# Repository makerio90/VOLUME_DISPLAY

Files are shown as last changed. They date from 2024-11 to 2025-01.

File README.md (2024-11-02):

# VOLUME_DISPLAY
this is a project i have been working on for the better part of a month now, this is only the first commit as i have dicided to add the project to github.

## The Idea:
i wanted to make a volumetric pov display. i got insperation from these projects:

- [this project is what kicked it off](https://hackaday.com/2024/09/09/doom-on-a-volumetric-display/)
- [and this served as insperation](https://hackaday.com/2021/02/21/volumetric-3d-television-is-here/)

both work off of the same principle: phisicly rotating an led matrix to create the sense of volume.

this seemed doable so i started work on schematics.

## theory of operation
cutting to the chase here: this is what the mainboard needs to do:

the main board is intended to drive a 32x16 led matrix at a high framerate (>1000fps).
new frames will be added to a framebuffer through a rs-485 bus. 12v power will also be supplied.
a hall effect sensor will provide a sync signal, allowing the board to make minor ajustments to its framerate.
most importently, this whole board rotates around. 12v and rs485 is fed through a slipring.

the entire board must be slowed to a stop in order for the rp2040 to be programmed.
whenever the usb port is plugged in. the rp2040 will be powered and in prog mode.
*the led drivers should be off when usb is plugged in!*

the board will be in the shape of a circle. the led matrix will be mounted vertically in the center via the attached pinheders.
because the board will likely be unbalanced, nuts and bolts will be added around in a circle to provide an option for balance.

## 4-layer stackup

top: high speed traces
in 1: signal, power & ground
in 2: Ground only
BOT: low speed, high current traces.

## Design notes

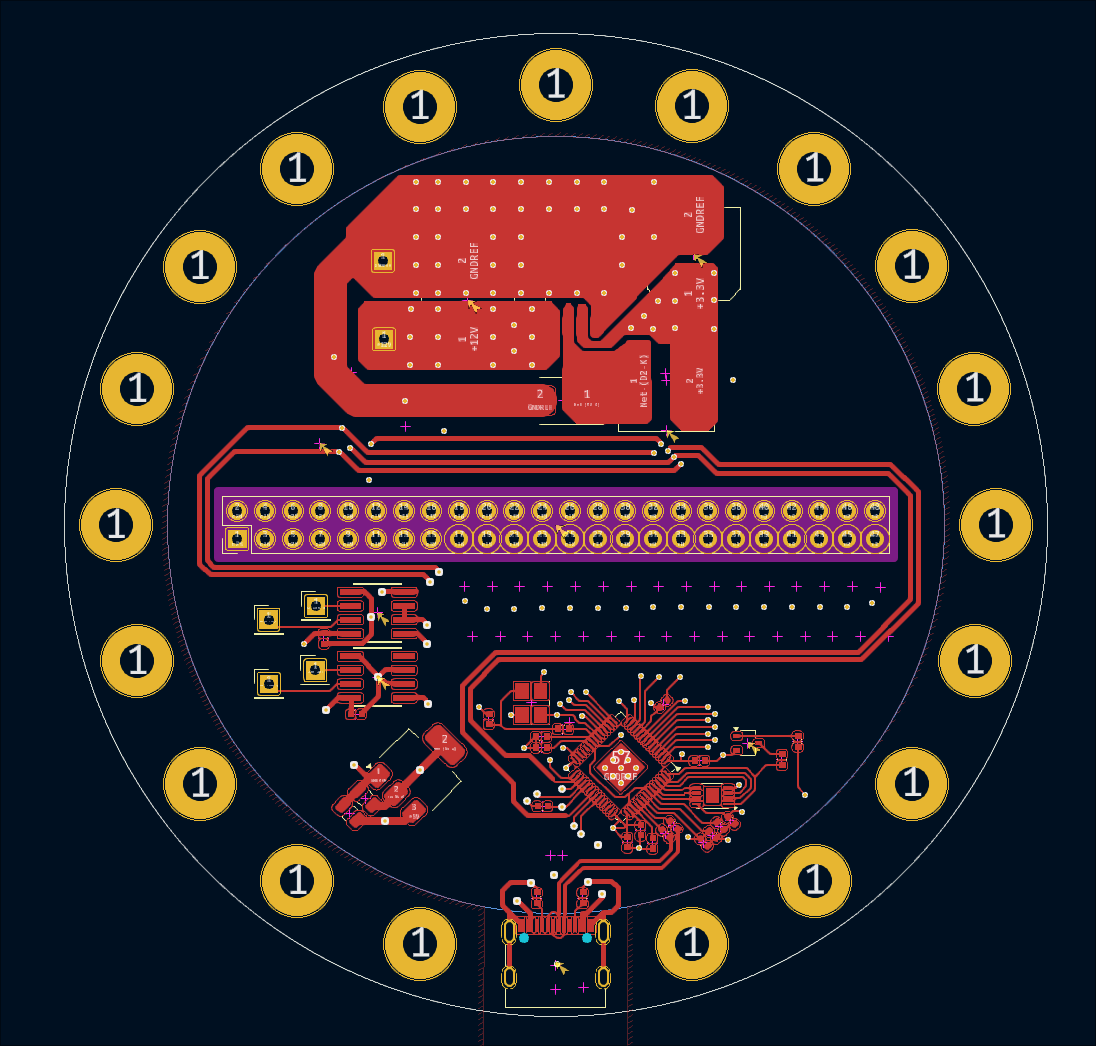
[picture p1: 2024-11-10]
forReview/TOP.png

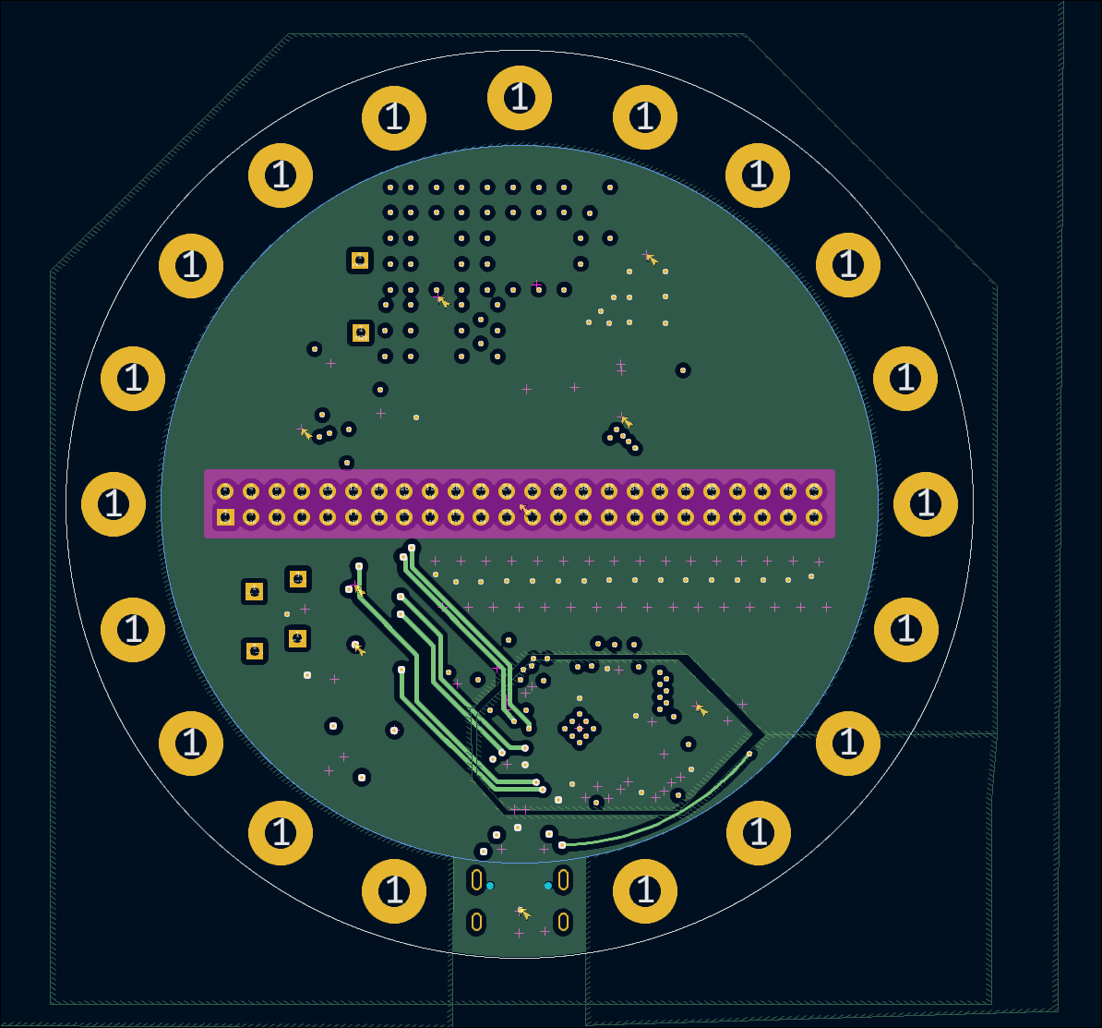
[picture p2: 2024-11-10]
forReview/in1.png

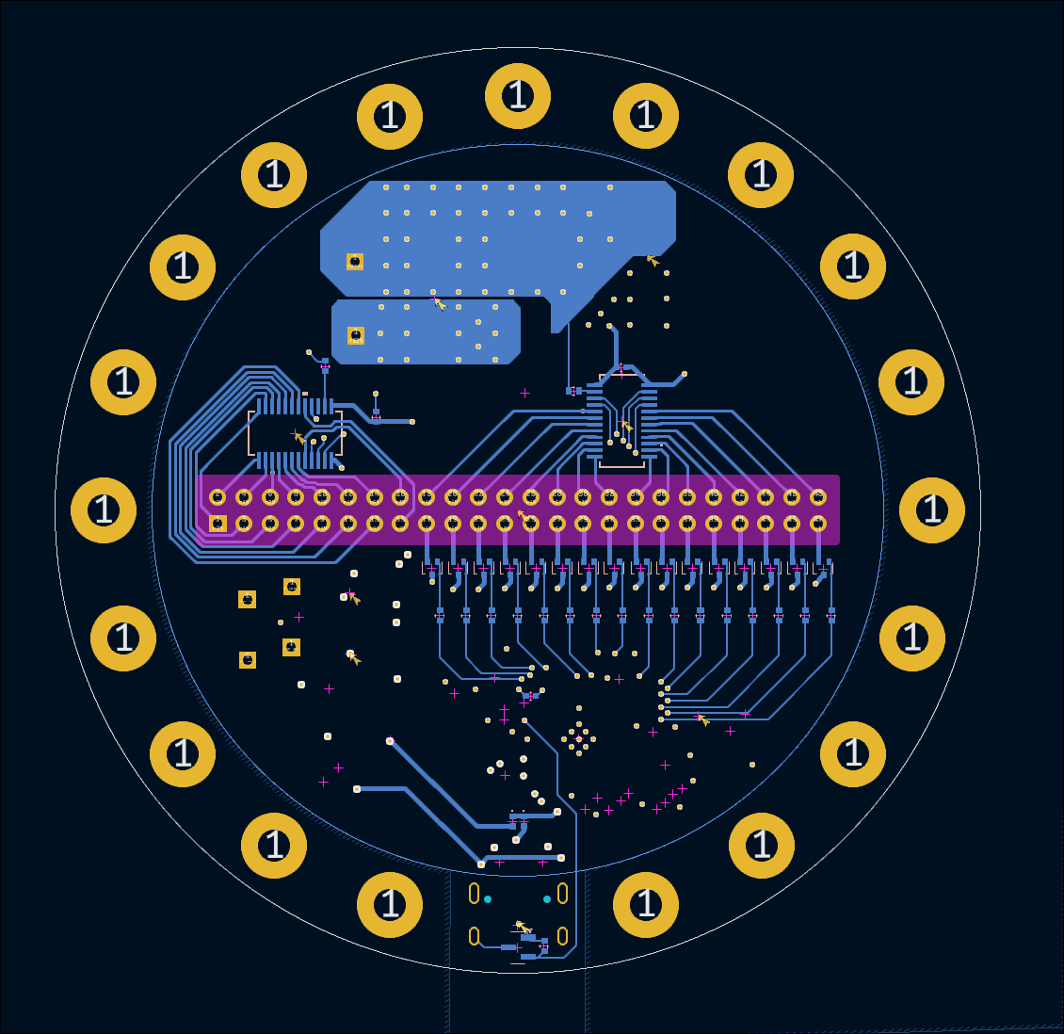
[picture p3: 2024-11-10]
forReview/BOT.png

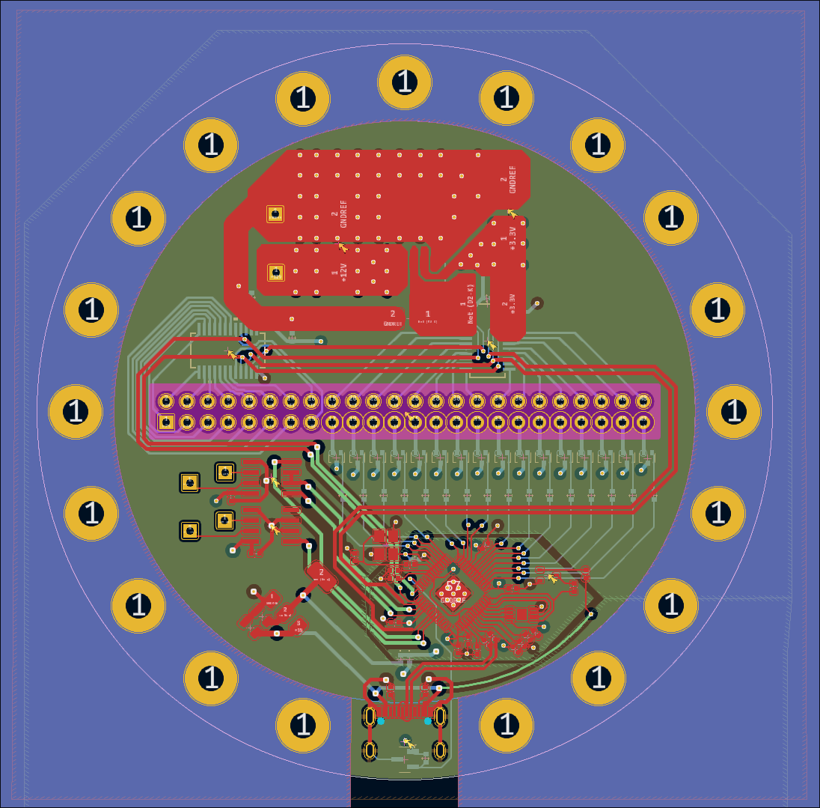
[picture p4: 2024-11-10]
forReview/all.png

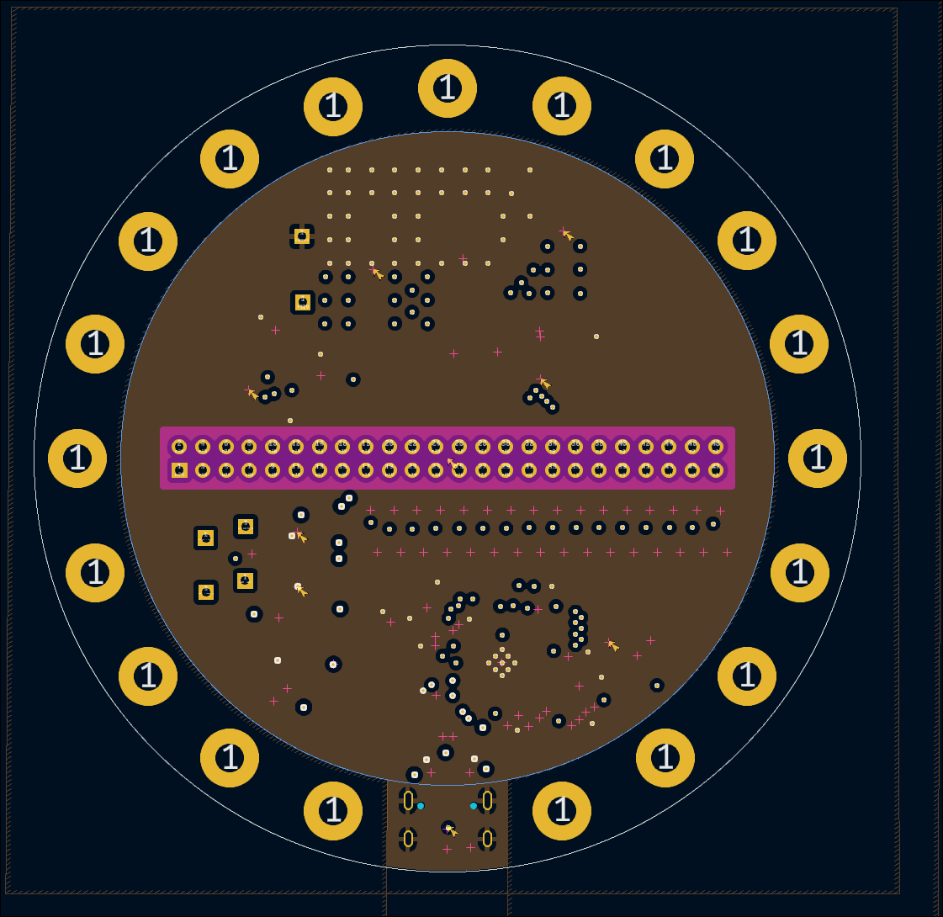
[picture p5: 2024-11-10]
forReview/in2.png

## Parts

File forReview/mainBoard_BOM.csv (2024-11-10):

Quantity | Comment | Designator | Footprint | LCSC PN | MPN | Manufacturer
2 | 10u | C1,C2 | Capacitor_SMD:C_0805_2012Metric | C15850 | CL21A106KAYNNNE | Samsung Electro-Mechanics
2 | 470uF | C16,C19 | Capacitor_SMD:C_Elec_8x10.2 | C343909 | EEEFP1C471AP | PANASONIC
2 | 15p | C17,C18 | Capacitor_SMD:C_0402_1005Metric | C307341 | CL05C150JB51PNC | Samsung Electro-Mechanics
14 | 100n | C3,C4,C6,C8,C9,C10,C11,C12,C13,C14,C15,C20,C21,C22 | Capacitor_SMD:C_0402_1005Metric | C1525 | CL05B104KO5NNNC | Samsung Electro-Mechanics
2 | 1u | C5,C7 | Capacitor_SMD:C_0402_1005Metric | C14445 | CL05A105KP5NNNC | Samsung Electro-Mechanics
1 | D_Schottky | D2 | Diode_SMD:D_SMB | C28642302 | TPNSR05F40NXT5G | TECH PUBLIC
2 | D | D1,D3 | Diode_SMD:D_0402_1005Metric | C703125 | LQW15AN12NH00D | Murata Electronics
1 | USB_C_Receptacle_USB2.0_16P | J1 | Connector_USB:USB_C_Receptacle_G-Switch_GT-USB-7010ASV | C2988369 | GT-USB-7010ASV | G-Switch
1 | SDCHA1V8040-470-R | L1 | Inductor_SMD:L_Coilcraft_XAL8080-XXX | C17221881 | SDCHA1V8040-470-R | EATON
2 | ST3485EBDR | Mm_rs485,RX_rs485 | footprints:SO-8_STM | C75809 | ST3485EBDR | STMicroelectronics
1 | BC846B,215 | Q1 | Package_TO_SOT_SMD:SOT-323_SC-70 | C87062 | BC846B,215 | Nexperia
16 | PMOS | Q2,Q3,Q4,Q5,Q6,Q7,Q8,Q9,Q10,Q11,Q12,Q13,Q14,Q15,Q16,Q17 | Package_TO_SOT_SMD:SOT-416 | C54876 | NTA4151PT1G | onsemi
2 | 27 | R1,R5 | Resistor_SMD:R_0402_1005Metric | C384351 | WR04X270JTL | Walsin Tech Corp
2 | 5.1k | R10,R11 | Resistor_SMD:R_0402_1005Metric | C5913162 | FCR0402F5K1 | VO
4 | 1k | R2,R6,R7,R9 | Resistor_SMD:R_0402_1005Metric | C102758 | RTT02102JTH | RALEC
2 | 2.65k | R3,R4 | Resistor_SMD:R_0402_1005Metric | C321166 | RC-02U2R61FT | RC-02U2R61FT
16 | 10 | R8,R12,R13,R14,R15,R16,R17,R18,R19,R20,R21,R22,R23,R24,R25,R26 | Resistor_SMD:R_0402_1005Metric | C100206 | CR0402FF10R0G | LIZ Elec
1 | W25Q128JVS | U1 | Package_DFN_QFN:WFDFPN-8-1EP_3x2mm_P0.5mm_EP1.25x1.35mm | C190862 | W25Q128JVPIQ | Winbond Electronics
1 | NCP1117-3.3_SOT223 | U5 | Package_TO_SOT_SMD:SOT-223-3_TabPin2 | C98965 | NCP1117ST12T3G | onsemi
1 | DRV5033FAxDBZ | U6 | Package_TO_SOT_SMD:SOT-23 | C2869057 | DRV5033FAQDBZR | Texas Instruments
1 | AP1509 | U7 | Package_SO:SOP-8_5.28x5.23mm_P1.27mm | C151822 | AP1509-SG-13 | Diodes Incorporated
1 | RP2040 | U8 | Package_DFN_QFN:QFN-56-1EP_7x7mm_P0.4mm_EP3.2x3.2mm | C2040 | RP2040 | Raspberry Pi
2 | TLC59283DBQR | U3,U4 | DBQ24_TEX:DBQ24_TEX | C702075 | TLC59283DBQR | Texas Instruments
1 | ABM8-272-T3 | Y2 | Crystal:Crystal_SMD_3225-4Pin_3.2x2.5mm | C20625731 | ABM8-272-T3 | Abracon LLC

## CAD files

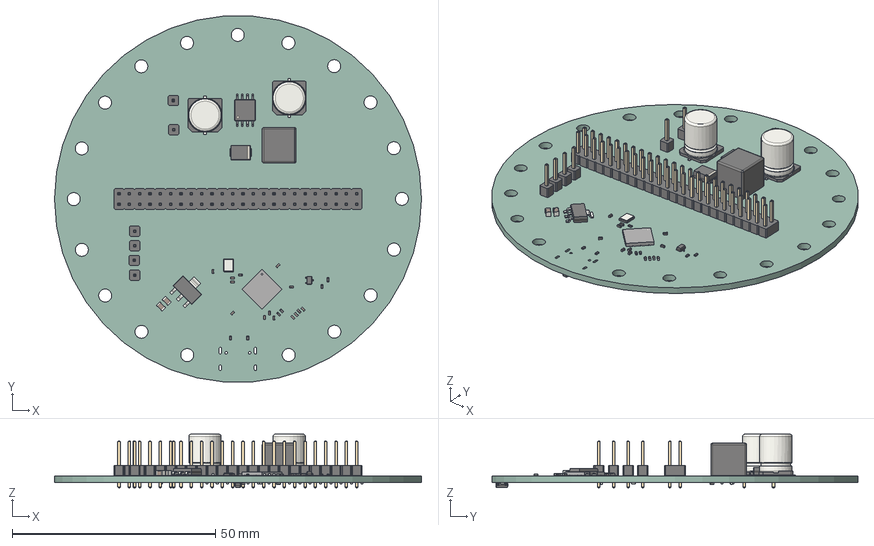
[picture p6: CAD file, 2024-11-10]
mainBoard.step
90.2 x 89.9 x 13.2 mm
CQ assembly
SOT_323_SC_70
C_0402_1005Metric x 16
C_Elec_8x102 x 2
R_0402_1005Metric x 26
C_0805_2012Metric x 2
PinHeader_2x24_P254mm_Vertical
Crystal_SMD_3225-4Pin_3.2x2.5mm
PinHeader_1x01_P254mm_Vertical x 6
D_SMB
SOP-8_5.28x5.23mm_P1.27mm
QFN_56_1EP_7x7mm_P04mm_EP32x32mm
SOT_223
SOT_23
mainBoard_PCB

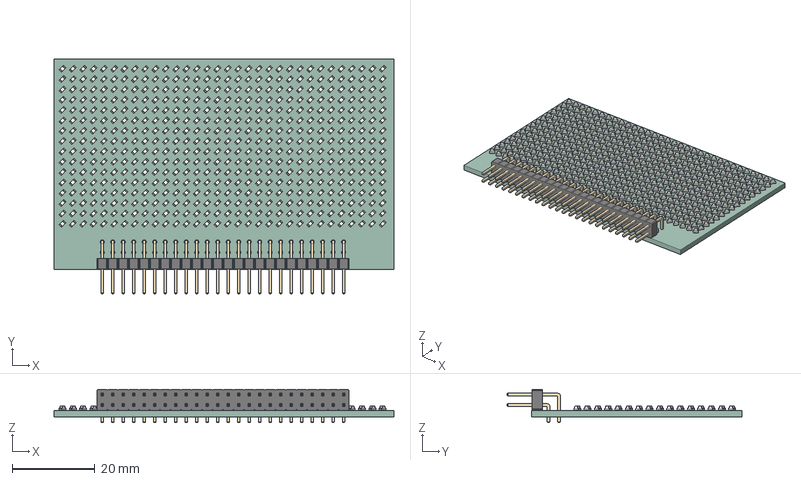
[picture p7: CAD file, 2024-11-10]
Matrix.step
82.3 x 56.8 x 8.08 mm
LED_0603_1608Metric x 512
PinHeader_2x24_P254mm_Horizontal
Matrix_PCB

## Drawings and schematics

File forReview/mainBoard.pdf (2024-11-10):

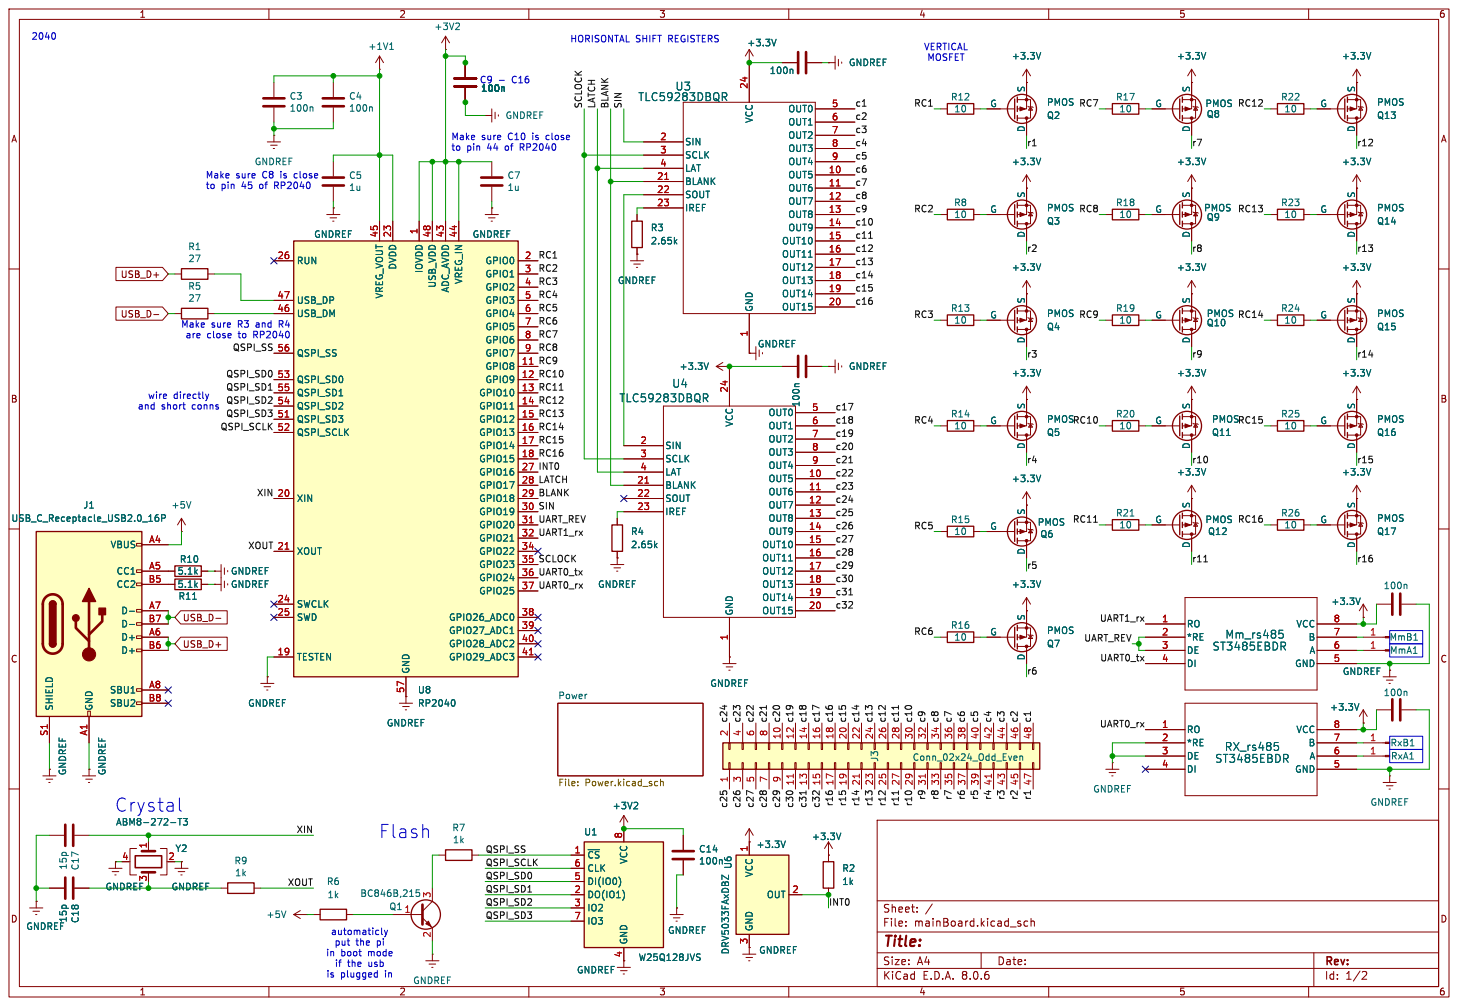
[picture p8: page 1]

HORISONTAL SHIFT REGISTERS wire directly and short conns Make sure C8 is close

to pin 45 of RP2040 Make sure R3 and R4

1 GPIO8 11 GPIO9 12 GPIO10 13 GPIO11 14 GPIO12 15 GPIO13 16 GPIO14 17 GPIO15 18 TESTEN 19 GPIO0 2 XIN 20 XOUT 21 DVDD 23 SWCLK 24 SWD 25 RUN 26 GPIO16 27 GPIO17 28 GPIO18 29 GPIO1 3 GPIO19 30 GPIO20 31 GPIO21 32 GPIO22 34 GPIO23 35 GPIO24 36 GPIO25 37 GPIO26_ADC0 38 GPIO27_ADC1 39 GPIO2 4 GPIO28_ADC2 40 GPIO29_ADC3 41 ADC_AVDD 43 VREG_IN 44 VREG_VOUT 45 USB_DM 46 USB_DP 47 USB_VDD 48 GPIO3 5 QSPI_SD3 51 QSPI_SCLK 52 QSPI_SD0 53 QSPI_SD2 54 QSPI_SD1 55 QSPI_SS 56 GND 57 GPIO4 6 GPIO5 7 GPIO6 8 GPIO7 9 U8 RP2040

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

Id: 1/2 Title: File: mainBoard.kicad_sch Sheet: / Power File: Power.kicad_sch

is plugged in Crystal

automaticly put the pi

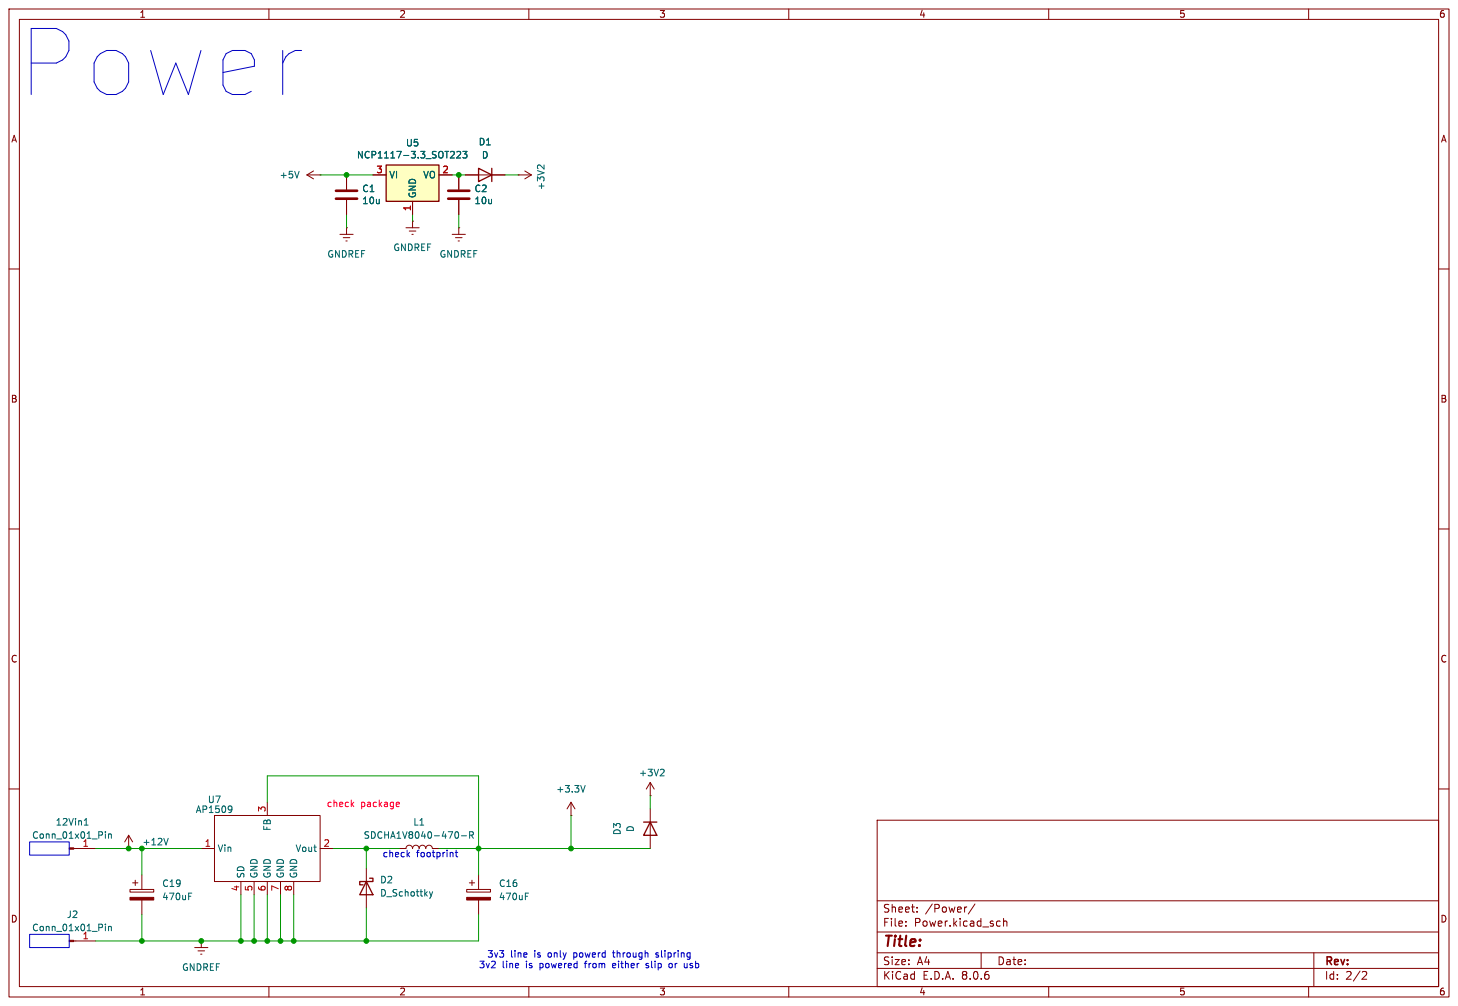
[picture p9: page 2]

Id: 2/2 Title: File: Power.kicad_sch Sheet: /Power/ D3D GNDREF GNDREF C1

check footprint check package

3v3 line is only powerd through slipring
3v2 line is powered from either slip or usb

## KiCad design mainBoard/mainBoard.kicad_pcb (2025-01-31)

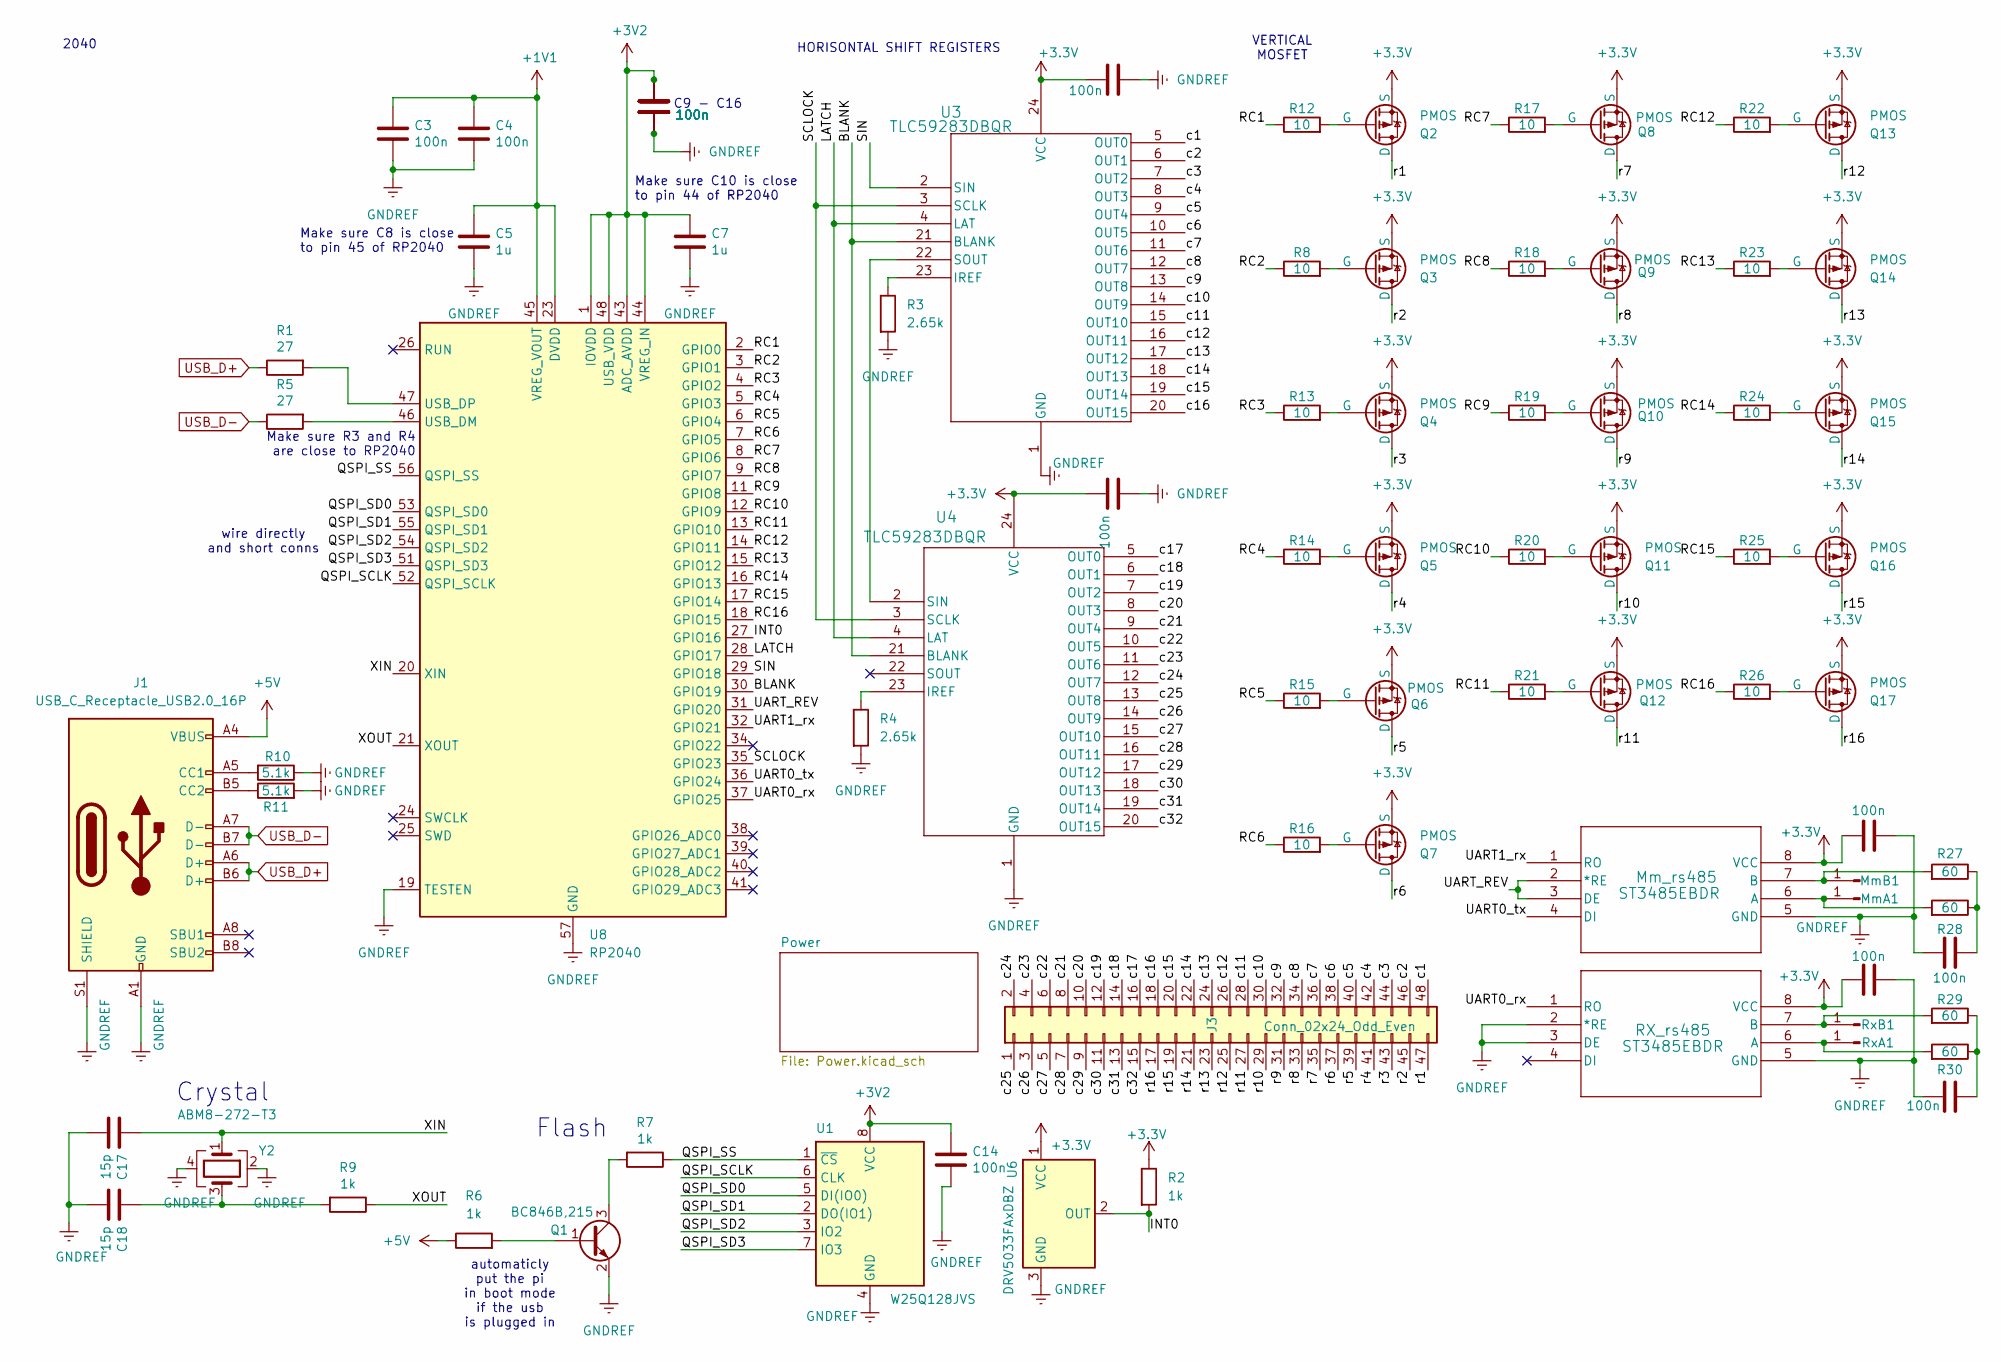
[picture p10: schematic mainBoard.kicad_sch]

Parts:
C3, C4, C6, C8, C9, C10, C11, C12, C13, C14, C15, C20, C21, C22, C23, C24: 100n; C_0402_1005Metric; MPN CL05B104KO5NNNC; LCSC PN C1525
C5, C7: 1u; C_0402_1005Metric; MPN CL05A105KP5NNNC; LCSC PN C14445
C17, C18: 15p; C_0402_1005Metric; MPN CL05C150JB51PNC; LCSC PN C307341
J1: USB_C_Receptacle_USB2.0_16P; USB_C_Receptacle_G-Switch_GT-USB-7010ASV; MPN GT-USB-7010ASV; LCSC PN C2988369
J3: Conn_02x24_Odd_Even; PinHeader_2x24_P2.54mm_Vertical
MmA1: Conn_01x01_Pin; PinHeader_1x01_P2.54mm_Vertical
MmB1: Conn_01x01_Pin; PinHeader_1x01_P2.54mm_Vertical
Mm_rs485: ST3485EBDR; SO-8_STM; MPN ST3485EBDR; LCSC PN C75809
Q1: BC846B,215; SOT-323_SC-70; MPN BC846B,215; LCSC PN C87062
Q2, Q3, Q4, Q5, Q6, Q7, Q8, Q9, Q10, Q11, Q12, Q13, Q14, Q15, Q16, Q17: PMOS; SOT-416; MPN NTA4151PT1G; LCSC PN C54876
R1, R5: 27; R_0402_1005Metric; MPN WR04X270JTL; LCSC PN C384351
R2, R6, R7, R9: 1k; R_0402_1005Metric; MPN RTT02102JTH; LCSC PN C102758
R3, R4: 2.65k; R_0402_1005Metric; MPN RC-02U2R61FT; LCSC PN C321166
R8, R12, R13, R14, R15, R16, R17, R18, R19, R20, R21, R22, R23, R24, R25, R26: 10; R_0402_1005Metric; MPN CR0402FF10R0G; LCSC PN C100206
R10, R11: 5.1k; R_0402_1005Metric; MPN FCR0402F5K1; LCSC PN C5913162
R27, R28, R29, R30: 60; R_0402_1005Metric; MPN CC0402KRX7R7BB104; LCSC PN C60474
RX_rs485: ST3485EBDR; SO-8_STM; MPN ST3485EBDR; LCSC PN C75809
RxA1: Conn_01x01_Pin; PinHeader_1x01_P2.54mm_Vertical
RxB1: Conn_01x01_Pin; PinHeader_1x01_P2.54mm_Vertical
U1: W25Q128JVS; WFDFPN-8-1EP_3x2mm_P0.5mm_EP1.25x1.35mm; MPN W25Q128JVPIQ; LCSC PN C190862
U3, U4: TLC59283DBQR; DBQ24_TEX; MPN TLC59283DBQR; LCSC PN C702075
U6: DRV5033FAxDBZ; SOT-23; MPN DRV5033FAQDBZR; LCSC PN C2869057
U8: RP2040; QFN-56-1EP_7x7mm_P0.4mm_EP3.2x3.2mm; MPN RP2040; LCSC PN C2040
Y2: ABM8-272-T3; Crystal_SMD_3225-4Pin_3.2x2.5mm; MPN ABM8-272-T3; LCSC PN C20625731

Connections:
+1V1: C3.1, C4.1, C5.1, U8.23 (DVDD), U8.45 (VREG_VOUT), U8.50 (DVDD)
+3.3V: C15.2, C20.2, C21.2, C22.2, Mm_rs485.8 (VCC), Q2.3 (S), Q3.3 (S), Q4.3 (S), Q5.3 (S), Q6.3 (S), Q7.3 (S), Q8.3 (S), Q9.3 (S), Q10.3 (S), Q11.3 (S), Q12.3 (S), Q13.3 (S), Q14.3 (S), Q15.3 (S), Q16.3 (S), Q17.3 (S), R2.1, RX_rs485.8 (VCC), U3.24 (VCC), U4.24 (VCC), U6.1 (VCC); also elsewhere on the board
+3V2: C6.1, C7.1, C8.1, C9.1, C10.1, C11.1, C12.1, C13.1, C14.1, U1.8 (VCC), U8.1 (IOVDD), U8.10 (IOVDD), U8.22 (IOVDD), U8.33 (IOVDD), U8.42 (IOVDD), U8.43 (ADC_AVDD), U8.44 (VREG_IN), U8.48 (USB_VDD), U8.49 (IOVDD); also elsewhere on the board
+5V: J1.A4 (VBUS), J1.A9 (VBUS), J1.B4 (VBUS), J1.B9 (VBUS), R6.1; also elsewhere on the board
/INT0: R2.2, U6.2 (OUT), U8.27 (GPIO16)
/LATCH: U3.4 (LAT), U4.4 (LAT), U8.28 (GPIO17)
/QSPI_SCLK: U1.6 (CLK), U8.52 (QSPI_SCLK)
/QSPI_SD0: U1.5 (DI(IO0)), U8.53 (QSPI_SD0)
/QSPI_SD1: U1.2 (DO(IO1)), U8.55 (QSPI_SD1)
/QSPI_SD2: U1.3 (IO2), U8.54 (QSPI_SD2)
/QSPI_SD3: U1.7 (IO3), U8.51 (QSPI_SD3)
/QSPI_SS: R7.1, U1.1 (~CS), U8.56 (QSPI_SS)
/RC1: R12.1, U8.2 (GPIO0)
/RC2: R8.1, U8.3 (GPIO1)
/RC3: R13.1, U8.4 (GPIO2)
/RC4: R14.1, U8.5 (GPIO3)
/RC5: R15.1, U8.6 (GPIO4)
/RC6: R16.1, U8.7 (GPIO5)
/RC7: R17.1, U8.8 (GPIO6)
/RC8: R18.1, U8.9 (GPIO7)
/RC9: R19.1, U8.11 (GPIO8)
/RC10: R20.1, U8.12 (GPIO9)
/RC11: R21.1, U8.13 (GPIO10)
/RC12: R22.1, U8.14 (GPIO11)
/RC13: R23.1, U8.15 (GPIO12)
/RC14: R24.1, U8.16 (GPIO13)
/RC15: R25.1, U8.17 (GPIO14)
/RC16: R26.1, U8.18 (GPIO15)
/SCLOCK: U3.3 (SCLK), U4.3 (SCLK), U8.35 (GPIO23)
/UART0_rx: RX_rs485.1 (RO), U8.37 (GPIO25)
/UART0_tx: Mm_rs485.4 (DI), U8.36 (GPIO24)
/UART1_rx: Mm_rs485.1 (RO), U8.32 (GPIO21)
/UART_REV: Mm_rs485.2 (*RE), Mm_rs485.3 (DE), U8.31 (GPIO20)
/XIN: C17.1, U8.20 (XIN), Y2.1
/XOUT: R9.1, U8.21 (XOUT)
/c1: J3.48, U3.5 (OUT0)
/c2: J3.46, U3.6 (OUT1)
/c3: J3.44, U3.7 (OUT2)
/c4: J3.42, U3.8 (OUT3)
/c5: J3.40, U3.9 (OUT4)
/c6: J3.38, U3.10 (OUT5)
/c7: J3.36, U3.11 (OUT6)
/c8: J3.34, U3.12 (OUT7)
/c9: J3.32, U3.13 (OUT8)
/c10: J3.30, U3.14 (OUT9)
/c11: J3.28, U3.15 (OUT10)
/c12: J3.26, U3.16 (OUT11)
/c13: J3.24, U3.17 (OUT12)
/c14: J3.22, U3.18 (OUT13)
/c15: J3.20, U3.19 (OUT14)
/c16: J3.18, U3.20 (OUT15)
/c17: J3.16, U4.5 (OUT0)
/c18: J3.14, U4.6 (OUT1)
/c19: J3.12, U4.7 (OUT2)
/c20: J3.10, U4.8 (OUT3)
/c21: J3.8, U4.9 (OUT4)
/c22: J3.6, U4.10 (OUT5)
/c23: J3.4, U4.11 (OUT6)
/c24: J3.2, U4.12 (OUT7)
/c25: J3.1, U4.13 (OUT8)
/c26: J3.3, U4.14 (OUT9)
/c27: J3.5, U4.15 (OUT10)
/c28: J3.7, U4.16 (OUT11)
/c29: J3.9, U4.17 (OUT12)
/c30: J3.11, U4.18 (OUT13)
/c31: J3.13, U4.19 (OUT14)
/c32: J3.15, U4.20 (OUT15)
/r1: J3.47, Q2.1 (D)
/r2: J3.45, Q3.1 (D)
/r3: J3.43, Q4.1 (D)
/r4: J3.41, Q5.1 (D)
/r5: J3.39, Q6.1 (D)
/r6: J3.37, Q7.1 (D)
/r7: J3.35, Q8.1 (D)
/r8: J3.33, Q9.1 (D)
/r9: J3.31, Q10.1 (D)
/r10: J3.29, Q11.1 (D)
/r11: J3.27, Q12.1 (D)
/r12: J3.25, Q13.1 (D)
/r13: J3.23, Q14.1 (D)
/r14: J3.21, Q15.1 (D)
/r15: J3.19, Q16.1 (D)
/r16: J3.17, Q17.1 (D)
GNDREF: C3.2, C4.2, C5.2, C6.2, C7.2, C8.2, C9.2, C10.2, C11.2, C12.2, C13.2, C14.2, C15.1, C17.2, C18.2, C20.1, C21.1, C22.1, C23.2, C24.1, J1.A1 (GND), J1.A12 (GND), J1.B1 (GND), J1.B12 (GND), J1.S1 (SHIELD), Mm_rs485.5 (GND), Q1.2 (E), R3.2, R4.2, R10.1, R11.2, RX_rs485.2 (*RE), RX_rs485.3 (DE), RX_rs485.5 (GND), U1.4 (GND), U3.1 (GND), U4.1 (GND), U6.3 (GND), U8.19 (TESTEN), U8.57 (GND), Y2.2, Y2.4; also elsewhere on the board
unnamed: C18.1, R9.2, Y2.3
unnamed: C23.1, R27.1, R28.1
unnamed: C24.2, R29.1, R30.1
unnamed: J1.A5 (CC1), R10.2
unnamed: J1.B5 (CC2), R11.1
unnamed: MmA1.1, Mm_rs485.6 (A), R28.2
unnamed: MmB1.1, Mm_rs485.7 (B), R27.2
unnamed: Q1.1 (B), R6.2
unnamed: Q1.3 (C), R7.2
unnamed: Q2.2 (G), R12.2
unnamed: Q3.2 (G), R8.2
unnamed: Q4.2 (G), R13.2
unnamed: Q5.2 (G), R14.2
unnamed: Q6.2 (G), R15.2
unnamed: Q7.2 (G), R16.2
unnamed: Q8.2 (G), R17.2
unnamed: Q9.2 (G), R18.2
unnamed: Q10.2 (G), R19.2
unnamed: Q11.2 (G), R20.2
unnamed: Q12.2 (G), R21.2
unnamed: Q13.2 (G), R22.2
unnamed: Q14.2 (G), R23.2
unnamed: Q15.2 (G), R24.2
unnamed: Q16.2 (G), R25.2
unnamed: Q17.2 (G), R26.2
unnamed: R30.2, RX_rs485.6 (A), RxA1.1
unnamed: R29.2, RX_rs485.7 (B), RxB1.1
unnamed: R3.1, U3.23 (IREF)
unnamed: U3.22 (SOUT), U4.2 (SIN)
unnamed: R4.1, U4.23 (IREF)
unnamed: R5.2, U8.46 (USB_DM)
unnamed: R1.2, U8.47 (USB_DP)
USB_D+: J1.A6 (D+), J1.B6 (D+), R1.1
USB_D-: J1.A7 (D-), J1.B7 (D-), R5.1

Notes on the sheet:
HORISONTAL SHIFT REGISTERS
Flash
Crystal
2040
VERTICAL MOSFET
automaticly put the pi in boot mode if the usb is plugged in
Make sure C10 is close to pin 44 of RP2040
wire directly and short conns
C9 - C16
Make sure C8 is close to pin 45 of RP2040
Make sure R3 and R4 are close to RP2040

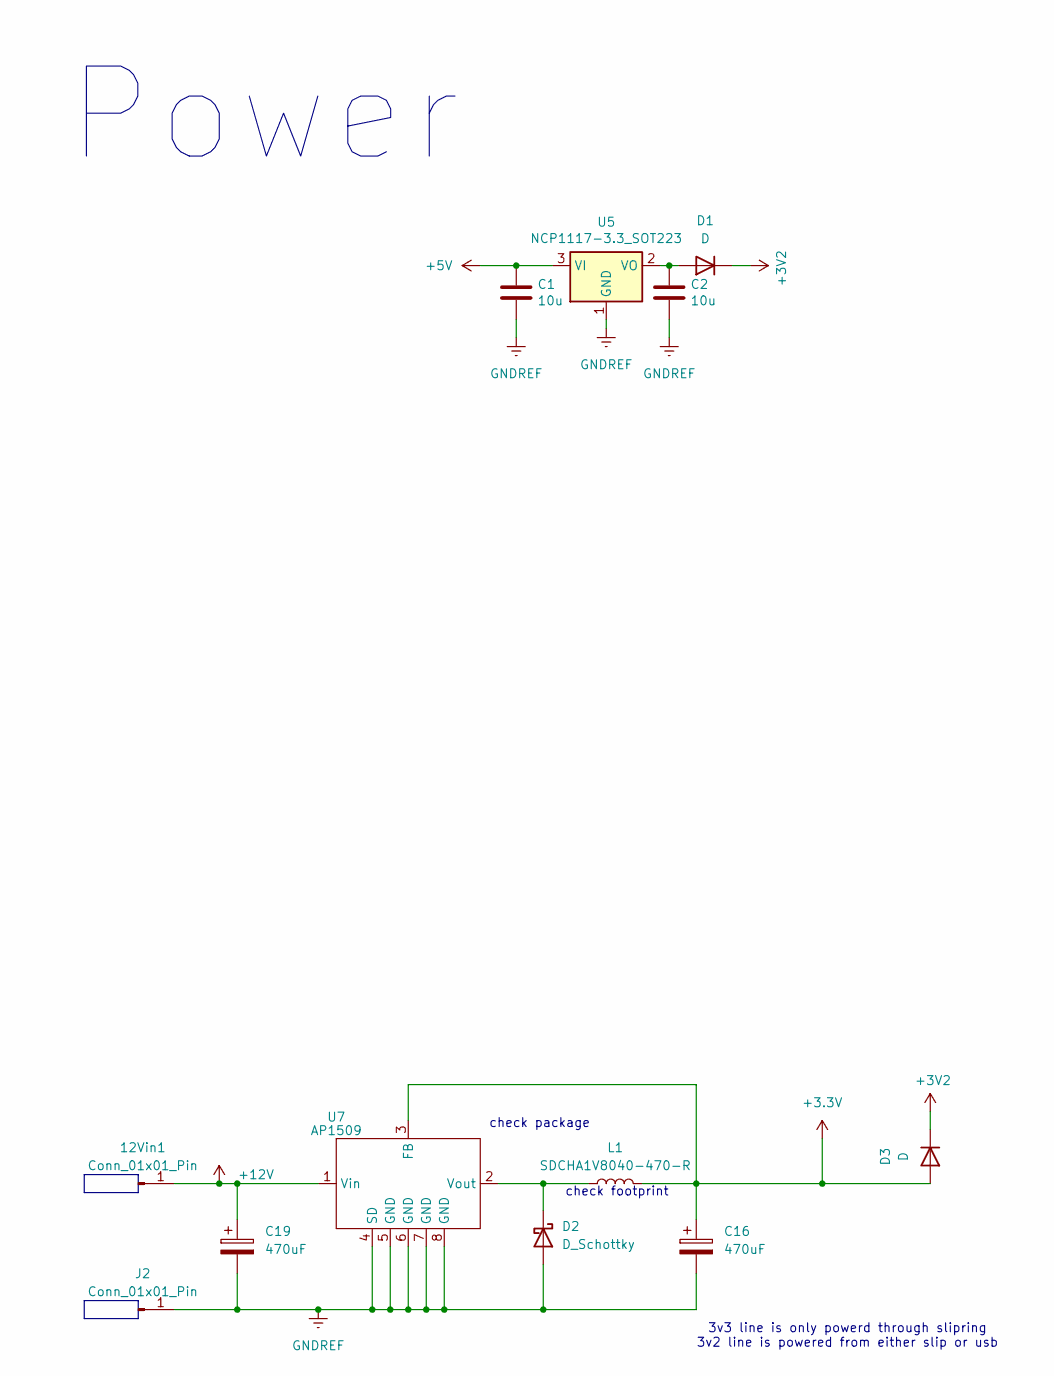
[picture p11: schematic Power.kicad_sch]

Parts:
12Vin1: Conn_01x01_Pin; PinHeader_1x01_P2.54mm_Vertical
C1, C2: 10u; C_0805_2012Metric; MPN CL21A106KAYNNNE; LCSC PN C15850
C16, C19: 470uF; C_Elec_8x10.2; MPN EEEFP1C471AP; LCSC PN C343909
D1, D3: D; D_0402_1005Metric; MPN LQW15AN12NH00D; LCSC PN C703125
D2: D_Schottky; D_SMB; MPN TPNSR05F40NXT5G; LCSC PN C28642302
J2: Conn_01x01_Pin; PinHeader_1x01_P2.54mm_Vertical
L1: SDCHA1V8040-470-R; L_Coilcraft_XAL8080-XXX; MPN SDCHA1V8040-470-R; LCSC PN C17221881
U5: NCP1117-3.3_SOT223; SOT-223-3_TabPin2; MPN NCP1117ST12T3G; LCSC PN C98965
U7: AP1509; SOP-8_5.28x5.23mm_P1.27mm; MPN AP1509-SG-13; LCSC PN C151822

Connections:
+3.3V: C16.1, D3.2 (A), L1.2, U7.3 (FB); also elsewhere on the board
+3V2: D1.1 (K), D3.1 (K); also elsewhere on the board
+5V: C1.1, U5.3 (VI); also elsewhere on the board
+12V: 12Vin1.1, C19.1, U7.1 (Vin)
GNDREF: C1.2, C2.2, C16.2, C19.2, D2.2 (A), J2.1, U5.1 (GND), U7.4 (SD), U7.5 (GND), U7.6 (GND), U7.7 (GND), U7.8 (GND); also elsewhere on the board
unnamed: C2.1, D1.2 (A), U5.2 (VO)
unnamed: D2.1 (K), L1.1, U7.2 (Vout)

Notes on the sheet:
check package
Power
check footprint
3v3 line is only powerd through slipring 3v2 line is powered from either slip or usb

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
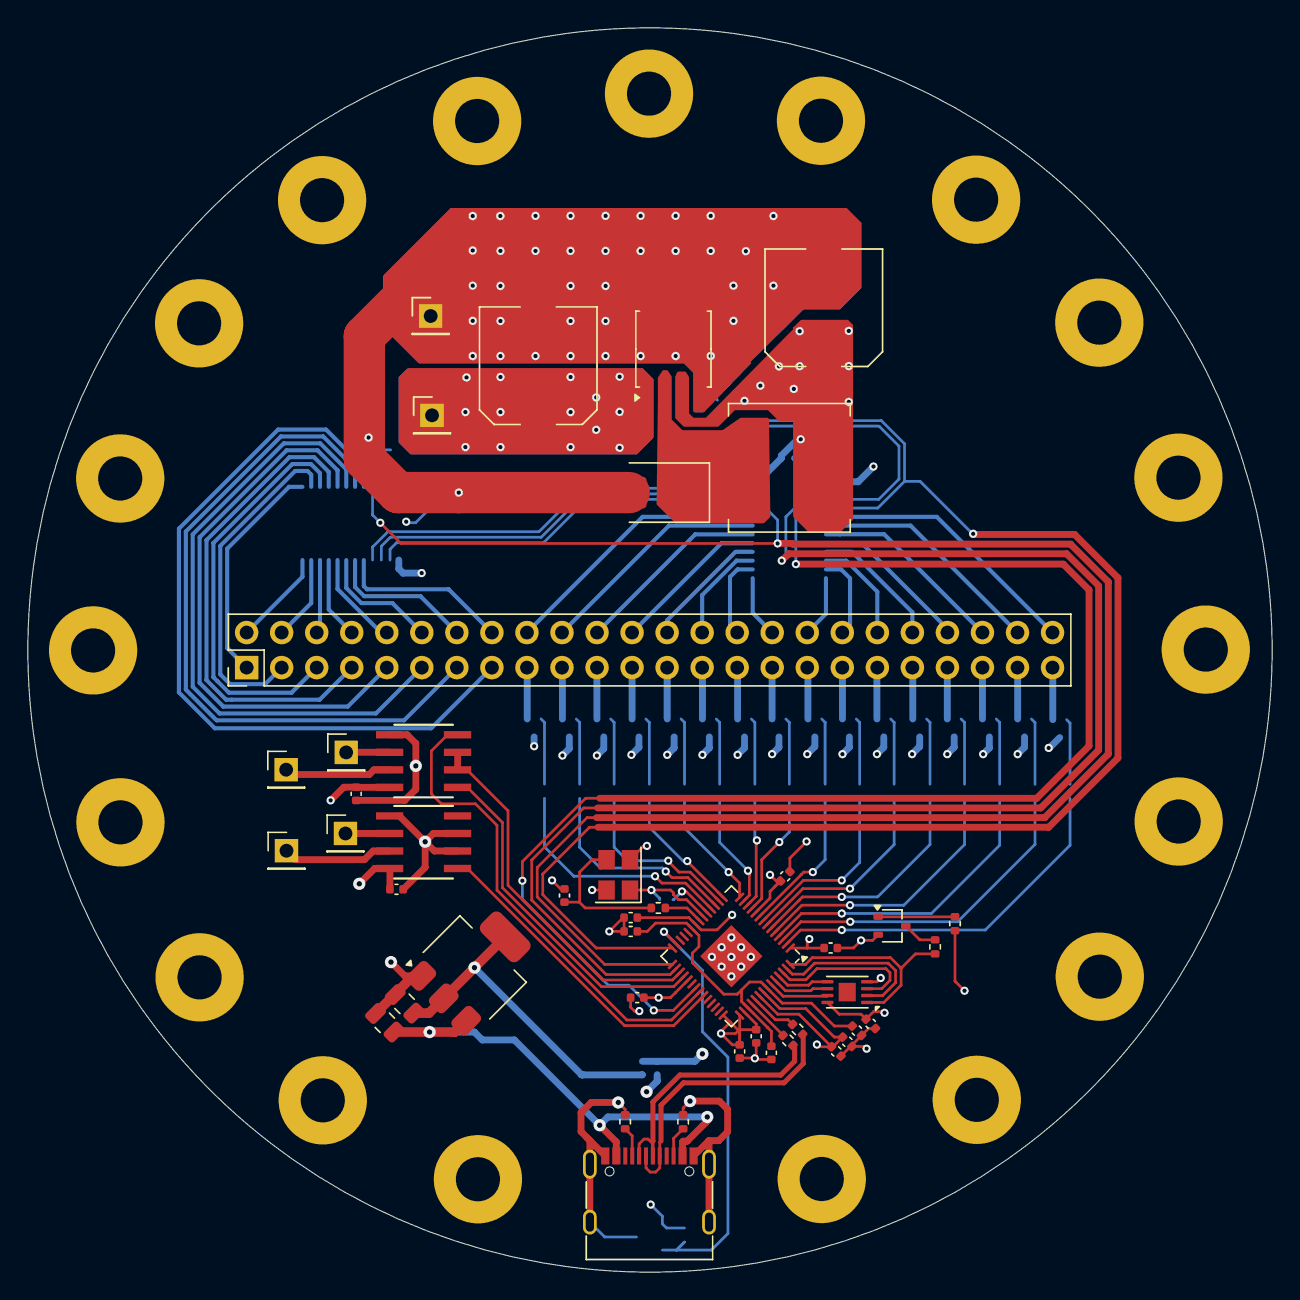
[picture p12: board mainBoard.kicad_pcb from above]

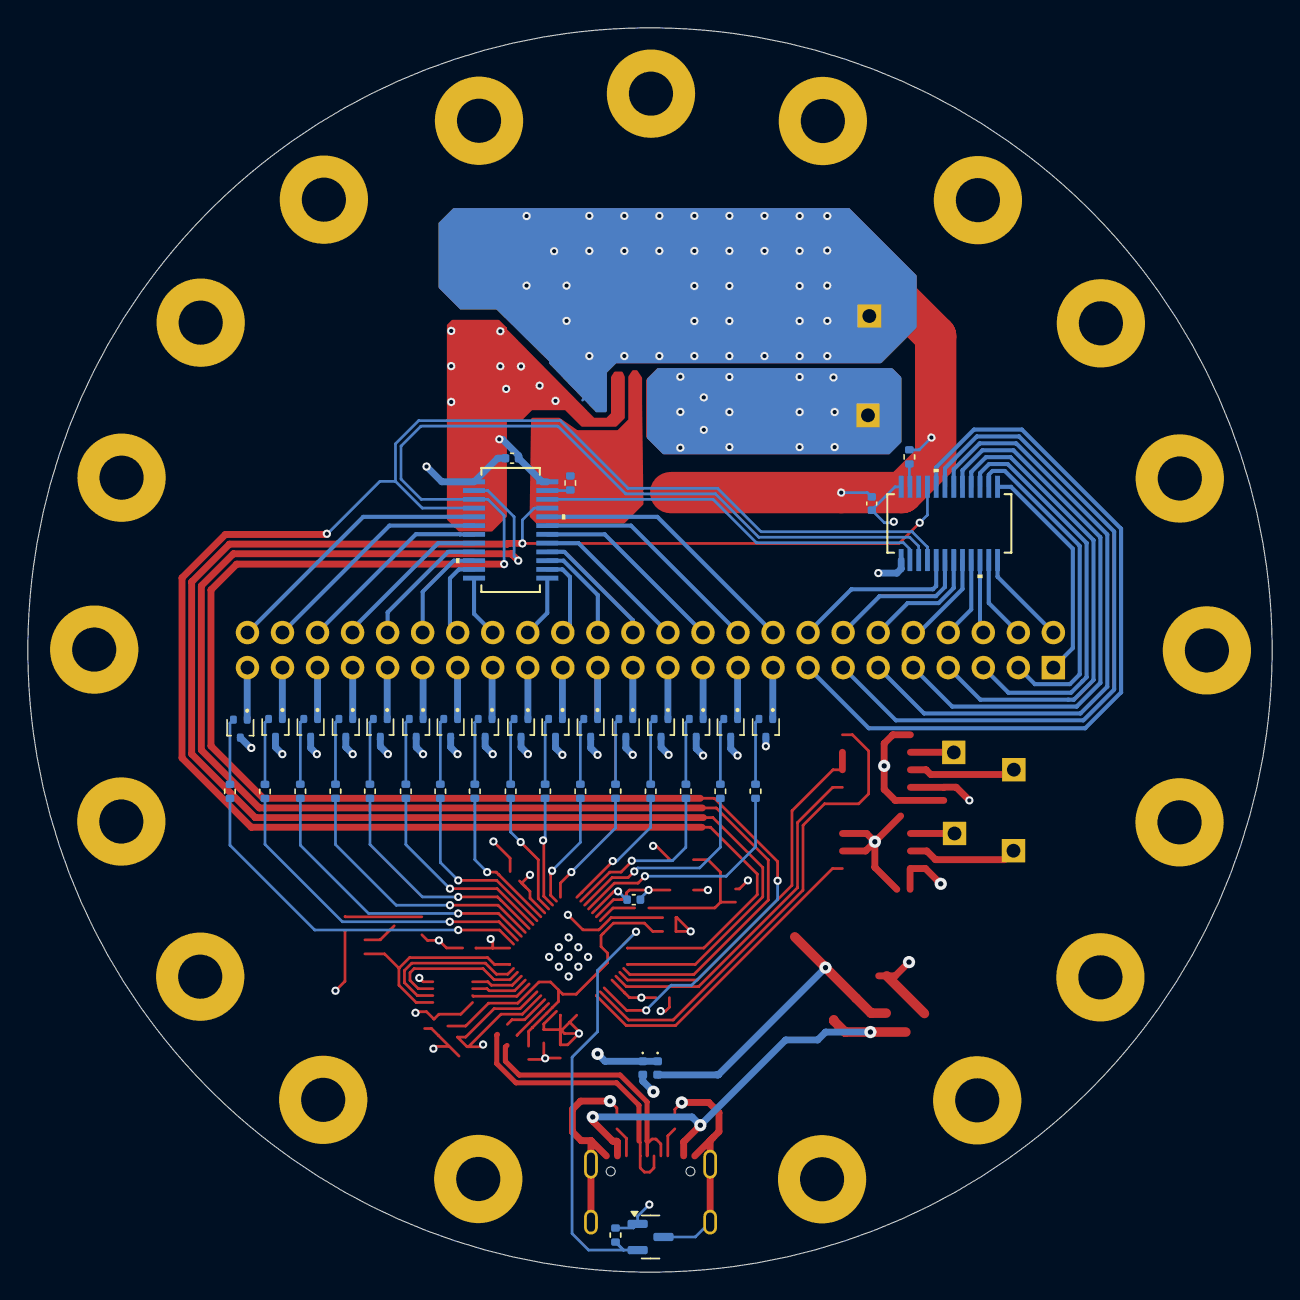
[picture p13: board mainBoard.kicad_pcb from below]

Board: 4 copper layers, 90.2 x 90.2 mm, 87 parts (43 on the bottom side), 121 nets.

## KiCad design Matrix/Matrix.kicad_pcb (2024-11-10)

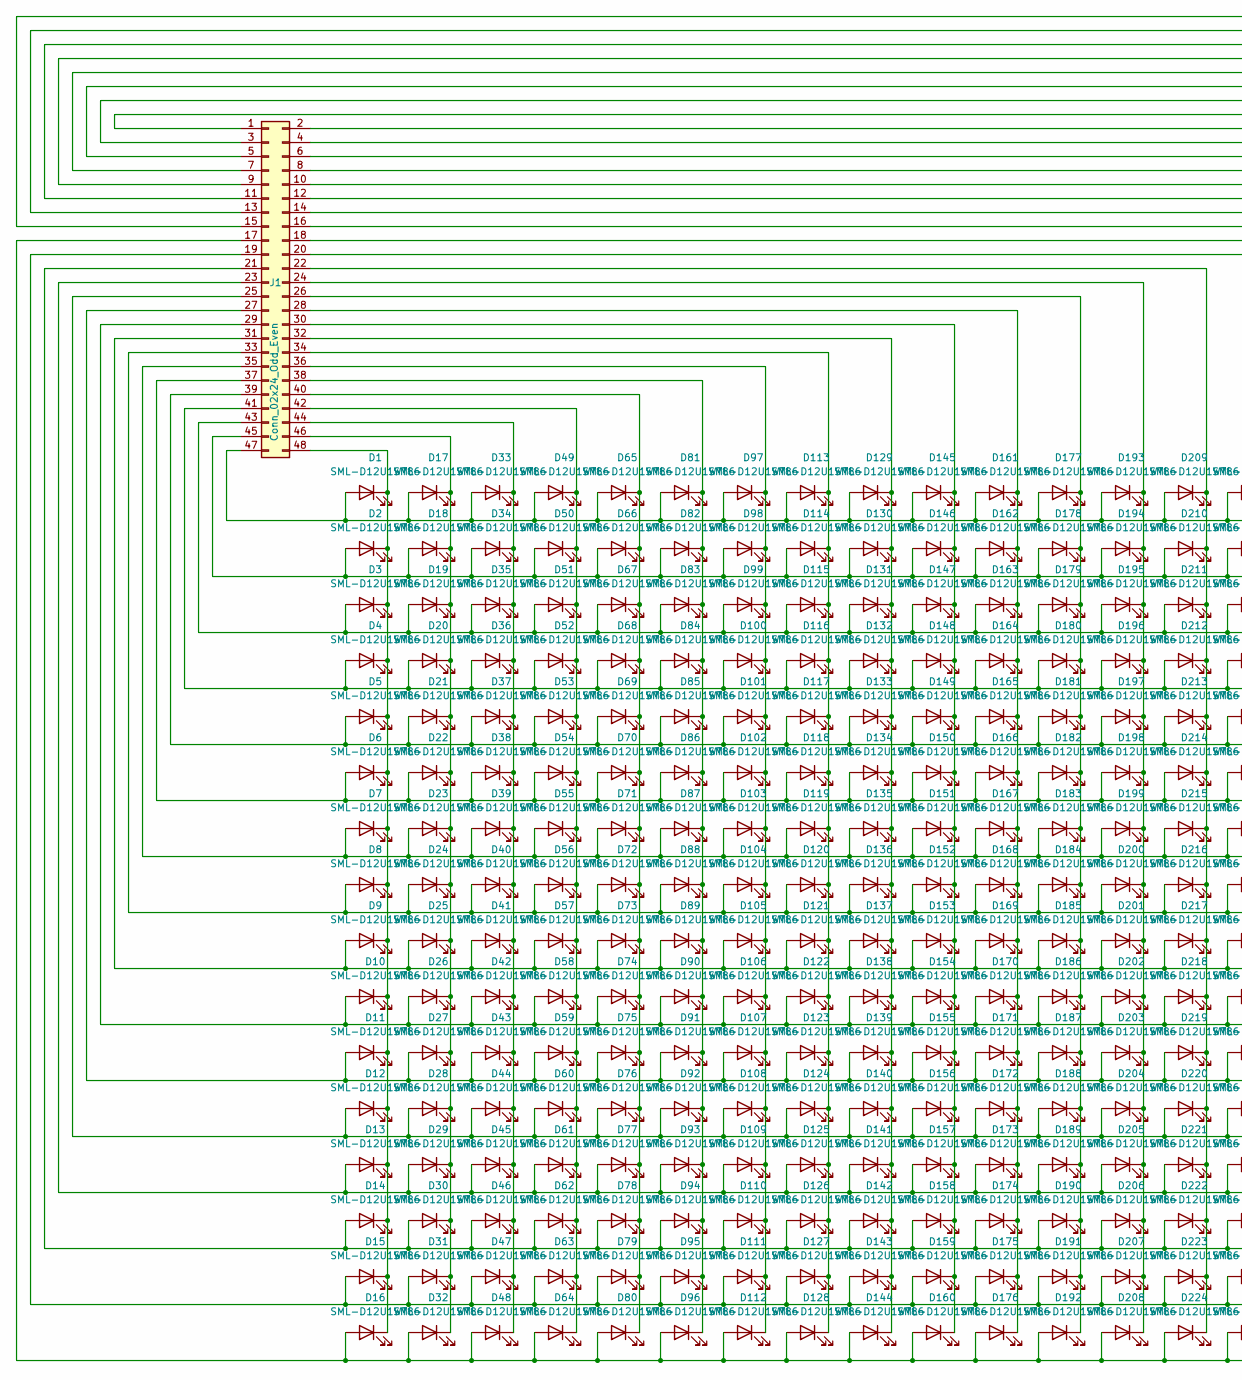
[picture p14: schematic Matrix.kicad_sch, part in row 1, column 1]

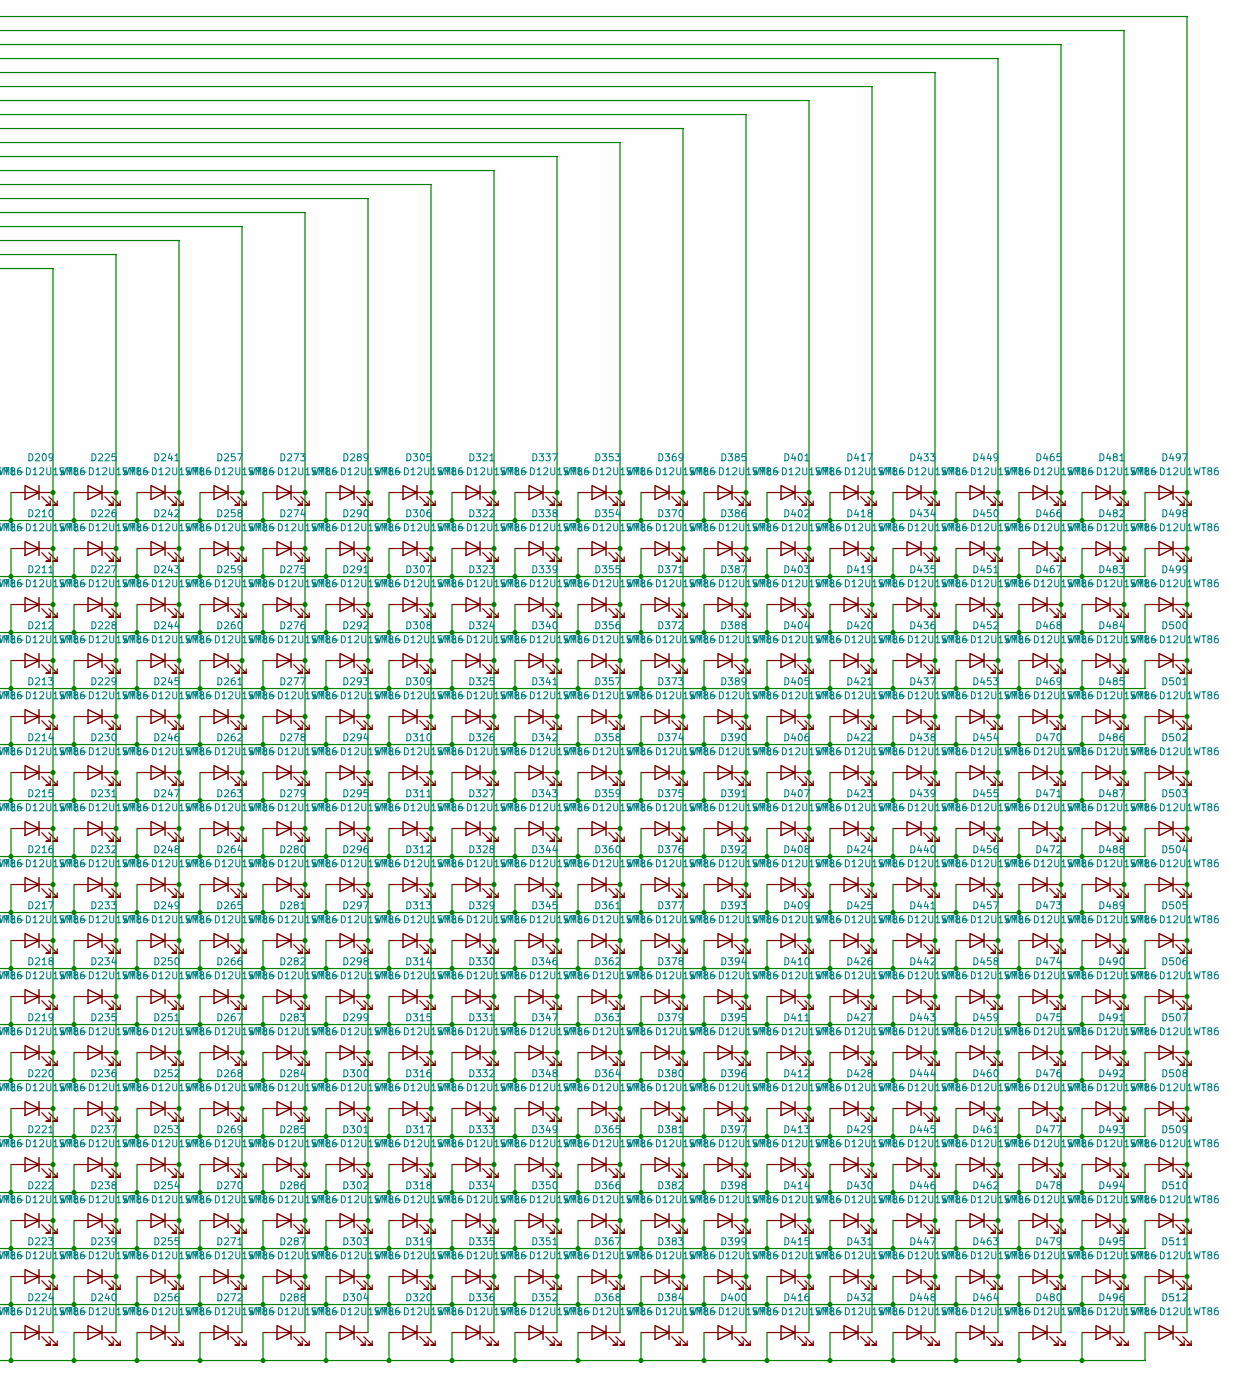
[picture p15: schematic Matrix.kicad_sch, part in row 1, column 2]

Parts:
D1, D2, D3, D4, D5, D6, D7, D8, D9, D10, D11, D12, D13, D14, D15, D16, D17, D18, D19, D20, D21, D22, D23, D24, D25, D26, D27, D28, D29, D30, D31, D32, D33, D34, D35, D36, D37, D38, D39, D40, D41, D42, D43, D44, D45, D46, D47, D48, D49, D50, D51, D52, D53, D54, D55, D56, D57, D58, D59, D60, D61, D62, D63, D64, D65, D66, D67, D68, D69, D70, D71, D72, D73, D74, D75, D76, D77, D78, D79, D80, D81, D82, D83, D84, D85, D86, D87, D88, D89, D90, D91, D92, D93, D94, D95, D96, D97, D98, D99, D100, D101, D102, D103, D104, D105, D106, D107, D108, D109, D110, D111, D112, D113, D114, D115, D116, D117, D118, D119, D120, D121, D122, D123, D124, D125, D126, D127, D128, D129, D130, D131, D132, D133, D134, D135, D136, D137, D138, D139, D140, D141, D142, D143, D144, D145, D146, D147, D148, D149, D150, D151, D152, D153, D154, D155, D156, D157, D158, D159, D160, D161, D162, D163, D164, D165, D166, D167, D168, D169, D170, D171, D172, D173, D174, D175, D176, D177, D178, D179, D180, D181, D182, D183, D184, D185, D186, D187, D188, D189, D190, D191, D192, D193, D194, D195, D196, D197, D198, D199, D200, D201, D202, D203, D204, D205, D206, D207, D208, D209, D210, D211, D212, D213, D214, D215, D216, D217, D218, D219, D220, D221, D222, D223, D224, D225, D226, D227, D228, D229, D230, D231, D232, D233, D234, D235, D236, D237, D238, D239, D240, D241, D242, D243, D244, D245, D246, D247, D248, D249, D250, D251, D252, D253, D254, D255, D256, D257, D258, D259, D260, D261, D262, D263, D264, D265, D266, D267, D268, D269, D270, D271, D272, D273, D274, D275, D276, D277, D278, D279, D280, D281, D282, D283, D284, D285, D286, D287, D288, D289, D290, D291, D292, D293, D294, D295, D296, D297, D298, D299, D300, D301, D302, D303, D304, D305, D306, D307, D308, D309, D310, D311, D312, D313, D314, D315, D316, D317, D318, D319, D320, D321, D322, D323, D324, D325, D326, D327, D328, D329, D330, D331, D332, D333, D334, D335, D336, D337, D338, D339, D340, D341, D342, D343, D344, D345, D346, D347, D348, D349, D350, D351, D352, D353, D354, D355, D356, D357, D358, D359, D360, D361, D362, D363, D364, D365, D366, D367, D368, D369, D370, D371, D372, D373, D374, D375, D376, D377, D378, D379, D380, D381, D382, D383, D384, D385, D386, D387, D388, D389, D390, D391, D392, D393, D394, D395, D396, D397, D398, D399, D400, D401, D402, D403, D404, D405, D406, D407, D408, D409, D410, D411, D412, D413, D414, D415, D416, D417, D418, D419, D420, D421, D422, D423, D424, D425, D426, D427, D428, D429, D430, D431, D432, D433, D434, D435, D436, D437, D438, D439, D440, D441, D442, D443, D444, D445, D446, D447, D448, D449, D450, D451, D452, D453, D454, D455, D456, D457, D458, D459, D460, D461, D462, D463, D464, D465, D466, D467, D468, D469, D470, D471, D472, D473, D474, D475, D476, D477, D478, D479, D480, D481, D482, D483, D484, D485, D486, D487, D488, D489, D490, D491, D492, D493, D494, D495, D496, D497, D498, D499, D500, D501, D502, D503, D504, D505, D506, D507, D508, D509, D510, D511, D512: SML-D12U1WT86; LED_0603_1608Metric
J1: Conn_02x24_Odd_Even; PinHeader_2x24_P2.54mm_Horizontal

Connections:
unnamed: D1.2 (A), D17.2 (A), D33.2 (A), D49.2 (A), D65.2 (A), D81.2 (A), D97.2 (A), D113.2 (A), D129.2 (A), D145.2 (A), D161.2 (A), D177.2 (A), D193.2 (A), D209.2 (A), D225.2 (A), D241.2 (A), D257.2 (A), D273.2 (A), D289.2 (A), D305.2 (A), D321.2 (A), D337.2 (A), D353.2 (A), D369.2 (A), D385.2 (A), D401.2 (A), D417.2 (A), D433.2 (A), D449.2 (A), D465.2 (A), D481.2 (A), D497.2 (A), J1.47
unnamed: D1.1 (K), D2.1 (K), D3.1 (K), D4.1 (K), D5.1 (K), D6.1 (K), D7.1 (K), D8.1 (K), D9.1 (K), D10.1 (K), D11.1 (K), D12.1 (K), D13.1 (K), D14.1 (K), D15.1 (K), D16.1 (K), J1.48
unnamed: D10.2 (A), D26.2 (A), D42.2 (A), D58.2 (A), D74.2 (A), D90.2 (A), D106.2 (A), D122.2 (A), D138.2 (A), D154.2 (A), D170.2 (A), D186.2 (A), D202.2 (A), D218.2 (A), D234.2 (A), D250.2 (A), D266.2 (A), D282.2 (A), D298.2 (A), D314.2 (A), D330.2 (A), D346.2 (A), D362.2 (A), D378.2 (A), D394.2 (A), D410.2 (A), D426.2 (A), D442.2 (A), D458.2 (A), D474.2 (A), D490.2 (A), D506.2 (A), J1.29
unnamed: D17.1 (K), D18.1 (K), D19.1 (K), D20.1 (K), D21.1 (K), D22.1 (K), D23.1 (K), D24.1 (K), D25.1 (K), D26.1 (K), D27.1 (K), D28.1 (K), D29.1 (K), D30.1 (K), D31.1 (K), D32.1 (K), J1.46
unnamed: D33.1 (K), D34.1 (K), D35.1 (K), D36.1 (K), D37.1 (K), D38.1 (K), D39.1 (K), D40.1 (K), D41.1 (K), D42.1 (K), D43.1 (K), D44.1 (K), D45.1 (K), D46.1 (K), D47.1 (K), D48.1 (K), J1.44
unnamed: D49.1 (K), D50.1 (K), D51.1 (K), D52.1 (K), D53.1 (K), D54.1 (K), D55.1 (K), D56.1 (K), D57.1 (K), D58.1 (K), D59.1 (K), D60.1 (K), D61.1 (K), D62.1 (K), D63.1 (K), D64.1 (K), J1.42
unnamed: D65.1 (K), D66.1 (K), D67.1 (K), D68.1 (K), D69.1 (K), D70.1 (K), D71.1 (K), D72.1 (K), D73.1 (K), D74.1 (K), D75.1 (K), D76.1 (K), D77.1 (K), D78.1 (K), D79.1 (K), D80.1 (K), J1.40
unnamed: D81.1 (K), D82.1 (K), D83.1 (K), D84.1 (K), D85.1 (K), D86.1 (K), D87.1 (K), D88.1 (K), D89.1 (K), D90.1 (K), D91.1 (K), D92.1 (K), D93.1 (K), D94.1 (K), D95.1 (K), D96.1 (K), J1.38
unnamed: D4.2 (A), D20.2 (A), D36.2 (A), D52.2 (A), D68.2 (A), D84.2 (A), D100.2 (A), D116.2 (A), D132.2 (A), D148.2 (A), D164.2 (A), D180.2 (A), D196.2 (A), D212.2 (A), D228.2 (A), D244.2 (A), D260.2 (A), D276.2 (A), D292.2 (A), D308.2 (A), D324.2 (A), D340.2 (A), D356.2 (A), D372.2 (A), D388.2 (A), D404.2 (A), D420.2 (A), D436.2 (A), D452.2 (A), D468.2 (A), D484.2 (A), D500.2 (A), J1.41
unnamed: D97.1 (K), D98.1 (K), D99.1 (K), D100.1 (K), D101.1 (K), D102.1 (K), D103.1 (K), D104.1 (K), D105.1 (K), D106.1 (K), D107.1 (K), D108.1 (K), D109.1 (K), D110.1 (K), D111.1 (K), D112.1 (K), J1.36
unnamed: D5.2 (A), D21.2 (A), D37.2 (A), D53.2 (A), D69.2 (A), D85.2 (A), D101.2 (A), D117.2 (A), D133.2 (A), D149.2 (A), D165.2 (A), D181.2 (A), D197.2 (A), D213.2 (A), D229.2 (A), D245.2 (A), D261.2 (A), D277.2 (A), D293.2 (A), D309.2 (A), D325.2 (A), D341.2 (A), D357.2 (A), D373.2 (A), D389.2 (A), D405.2 (A), D421.2 (A), D437.2 (A), D453.2 (A), D469.2 (A), D485.2 (A), D501.2 (A), J1.39
unnamed: D6.2 (A), D22.2 (A), D38.2 (A), D54.2 (A), D70.2 (A), D86.2 (A), D102.2 (A), D118.2 (A), D134.2 (A), D150.2 (A), D166.2 (A), D182.2 (A), D198.2 (A), D214.2 (A), D230.2 (A), D246.2 (A), D262.2 (A), D278.2 (A), D294.2 (A), D310.2 (A), D326.2 (A), D342.2 (A), D358.2 (A), D374.2 (A), D390.2 (A), D406.2 (A), D422.2 (A), D438.2 (A), D454.2 (A), D470.2 (A), D486.2 (A), D502.2 (A), J1.37
unnamed: D7.2 (A), D23.2 (A), D39.2 (A), D55.2 (A), D71.2 (A), D87.2 (A), D103.2 (A), D119.2 (A), D135.2 (A), D151.2 (A), D167.2 (A), D183.2 (A), D199.2 (A), D215.2 (A), D231.2 (A), D247.2 (A), D263.2 (A), D279.2 (A), D295.2 (A), D311.2 (A), D327.2 (A), D343.2 (A), D359.2 (A), D375.2 (A), D391.2 (A), D407.2 (A), D423.2 (A), D439.2 (A), D455.2 (A), D471.2 (A), D487.2 (A), D503.2 (A), J1.35
unnamed: D8.2 (A), D24.2 (A), D40.2 (A), D56.2 (A), D72.2 (A), D88.2 (A), D104.2 (A), D120.2 (A), D136.2 (A), D152.2 (A), D168.2 (A), D184.2 (A), D200.2 (A), D216.2 (A), D232.2 (A), D248.2 (A), D264.2 (A), D280.2 (A), D296.2 (A), D312.2 (A), D328.2 (A), D344.2 (A), D360.2 (A), D376.2 (A), D392.2 (A), D408.2 (A), D424.2 (A), D440.2 (A), D456.2 (A), D472.2 (A), D488.2 (A), D504.2 (A), J1.33
unnamed: D9.2 (A), D25.2 (A), D41.2 (A), D57.2 (A), D73.2 (A), D89.2 (A), D105.2 (A), D121.2 (A), D137.2 (A), D153.2 (A), D169.2 (A), D185.2 (A), D201.2 (A), D217.2 (A), D233.2 (A), D249.2 (A), D265.2 (A), D281.2 (A), D297.2 (A), D313.2 (A), D329.2 (A), D345.2 (A), D361.2 (A), D377.2 (A), D393.2 (A), D409.2 (A), D425.2 (A), D441.2 (A), D457.2 (A), D473.2 (A), D489.2 (A), D505.2 (A), J1.31
unnamed: D11.2 (A), D27.2 (A), D43.2 (A), D59.2 (A), D75.2 (A), D91.2 (A), D107.2 (A), D123.2 (A), D139.2 (A), D155.2 (A), D171.2 (A), D187.2 (A), D203.2 (A), D219.2 (A), D235.2 (A), D251.2 (A), D267.2 (A), D283.2 (A), D299.2 (A), D315.2 (A), D331.2 (A), D347.2 (A), D363.2 (A), D379.2 (A), D395.2 (A), D411.2 (A), D427.2 (A), D443.2 (A), D459.2 (A), D475.2 (A), D491.2 (A), D507.2 (A), J1.27
unnamed: D12.2 (A), D28.2 (A), D44.2 (A), D60.2 (A), D76.2 (A), D92.2 (A), D108.2 (A), D124.2 (A), D140.2 (A), D156.2 (A), D172.2 (A), D188.2 (A), D204.2 (A), D220.2 (A), D236.2 (A), D252.2 (A), D268.2 (A), D284.2 (A), D300.2 (A), D316.2 (A), D332.2 (A), D348.2 (A), D364.2 (A), D380.2 (A), D396.2 (A), D412.2 (A), D428.2 (A), D444.2 (A), D460.2 (A), D476.2 (A), D492.2 (A), D508.2 (A), J1.25
unnamed: D13.2 (A), D29.2 (A), D45.2 (A), D61.2 (A), D77.2 (A), D93.2 (A), D109.2 (A), D125.2 (A), D141.2 (A), D157.2 (A), D173.2 (A), D189.2 (A), D205.2 (A), D221.2 (A), D237.2 (A), D253.2 (A), D269.2 (A), D285.2 (A), D301.2 (A), D317.2 (A), D333.2 (A), D349.2 (A), D365.2 (A), D381.2 (A), D397.2 (A), D413.2 (A), D429.2 (A), D445.2 (A), D461.2 (A), D477.2 (A), D493.2 (A), D509.2 (A), J1.23
unnamed: D14.2 (A), D30.2 (A), D46.2 (A), D62.2 (A), D78.2 (A), D94.2 (A), D110.2 (A), D126.2 (A), D142.2 (A), D158.2 (A), D174.2 (A), D190.2 (A), D206.2 (A), D222.2 (A), D238.2 (A), D254.2 (A), D270.2 (A), D286.2 (A), D302.2 (A), D318.2 (A), D334.2 (A), D350.2 (A), D366.2 (A), D382.2 (A), D398.2 (A), D414.2 (A), D430.2 (A), D446.2 (A), D462.2 (A), D478.2 (A), D494.2 (A), D510.2 (A), J1.21
unnamed: D15.2 (A), D31.2 (A), D47.2 (A), D63.2 (A), D79.2 (A), D95.2 (A), D111.2 (A), D127.2 (A), D143.2 (A), D159.2 (A), D175.2 (A), D191.2 (A), D207.2 (A), D223.2 (A), D239.2 (A), D255.2 (A), D271.2 (A), D287.2 (A), D303.2 (A), D319.2 (A), D335.2 (A), D351.2 (A), D367.2 (A), D383.2 (A), D399.2 (A), D415.2 (A), D431.2 (A), D447.2 (A), D463.2 (A), D479.2 (A), D495.2 (A), D511.2 (A), J1.19
unnamed: D16.2 (A), D32.2 (A), D48.2 (A), D64.2 (A), D80.2 (A), D96.2 (A), D112.2 (A), D128.2 (A), D144.2 (A), D160.2 (A), D176.2 (A), D192.2 (A), D208.2 (A), D224.2 (A), D240.2 (A), D256.2 (A), D272.2 (A), D288.2 (A), D304.2 (A), D320.2 (A), D336.2 (A), D352.2 (A), D368.2 (A), D384.2 (A), D400.2 (A), D416.2 (A), D432.2 (A), D448.2 (A), D464.2 (A), D480.2 (A), D496.2 (A), D512.2 (A), J1.17
unnamed: D113.1 (K), D114.1 (K), D115.1 (K), D116.1 (K), D117.1 (K), D118.1 (K), D119.1 (K), D120.1 (K), D121.1 (K), D122.1 (K), D123.1 (K), D124.1 (K), D125.1 (K), D126.1 (K), D127.1 (K), D128.1 (K), J1.34
unnamed: D2.2 (A), D18.2 (A), D34.2 (A), D50.2 (A), D66.2 (A), D82.2 (A), D98.2 (A), D114.2 (A), D130.2 (A), D146.2 (A), D162.2 (A), D178.2 (A), D194.2 (A), D210.2 (A), D226.2 (A), D242.2 (A), D258.2 (A), D274.2 (A), D290.2 (A), D306.2 (A), D322.2 (A), D338.2 (A), D354.2 (A), D370.2 (A), D386.2 (A), D402.2 (A), D418.2 (A), D434.2 (A), D450.2 (A), D466.2 (A), D482.2 (A), D498.2 (A), J1.45
unnamed: D3.2 (A), D19.2 (A), D35.2 (A), D51.2 (A), D67.2 (A), D83.2 (A), D99.2 (A), D115.2 (A), D131.2 (A), D147.2 (A), D163.2 (A), D179.2 (A), D195.2 (A), D211.2 (A), D227.2 (A), D243.2 (A), D259.2 (A), D275.2 (A), D291.2 (A), D307.2 (A), D323.2 (A), D339.2 (A), D355.2 (A), D371.2 (A), D387.2 (A), D403.2 (A), D419.2 (A), D435.2 (A), D451.2 (A), D467.2 (A), D483.2 (A), D499.2 (A), J1.43
unnamed: D129.1 (K), D130.1 (K), D131.1 (K), D132.1 (K), D133.1 (K), D134.1 (K), D135.1 (K), D136.1 (K), D137.1 (K), D138.1 (K), D139.1 (K), D140.1 (K), D141.1 (K), D142.1 (K), D143.1 (K), D144.1 (K), J1.32
unnamed: D145.1 (K), D146.1 (K), D147.1 (K), D148.1 (K), D149.1 (K), D150.1 (K), D151.1 (K), D152.1 (K), D153.1 (K), D154.1 (K), D155.1 (K), D156.1 (K), D157.1 (K), D158.1 (K), D159.1 (K), D160.1 (K), J1.30
unnamed: D161.1 (K), D162.1 (K), D163.1 (K), D164.1 (K), D165.1 (K), D166.1 (K), D167.1 (K), D168.1 (K), D169.1 (K), D170.1 (K), D171.1 (K), D172.1 (K), D173.1 (K), D174.1 (K), D175.1 (K), D176.1 (K), J1.28
unnamed: D177.1 (K), D178.1 (K), D179.1 (K), D180.1 (K), D181.1 (K), D182.1 (K), D183.1 (K), D184.1 (K), D185.1 (K), D186.1 (K), D187.1 (K), D188.1 (K), D189.1 (K), D190.1 (K), D191.1 (K), D192.1 (K), J1.26
unnamed: D193.1 (K), D194.1 (K), D195.1 (K), D196.1 (K), D197.1 (K), D198.1 (K), D199.1 (K), D200.1 (K), D201.1 (K), D202.1 (K), D203.1 (K), D204.1 (K), D205.1 (K), D206.1 (K), D207.1 (K), D208.1 (K), J1.24
unnamed: D209.1 (K), D210.1 (K), D211.1 (K), D212.1 (K), D213.1 (K), D214.1 (K), D215.1 (K), D216.1 (K), D217.1 (K), D218.1 (K), D219.1 (K), D220.1 (K), D221.1 (K), D222.1 (K), D223.1 (K), D224.1 (K), J1.22
unnamed: D225.1 (K), D226.1 (K), D227.1 (K), D228.1 (K), D229.1 (K), D230.1 (K), D231.1 (K), D232.1 (K), D233.1 (K), D234.1 (K), D235.1 (K), D236.1 (K), D237.1 (K), D238.1 (K), D239.1 (K), D240.1 (K), J1.20
unnamed: D241.1 (K), D242.1 (K), D243.1 (K), D244.1 (K), D245.1 (K), D246.1 (K), D247.1 (K), D248.1 (K), D249.1 (K), D250.1 (K), D251.1 (K), D252.1 (K), D253.1 (K), D254.1 (K), D255.1 (K), D256.1 (K), J1.18
unnamed: D257.1 (K), D258.1 (K), D259.1 (K), D260.1 (K), D261.1 (K), D262.1 (K), D263.1 (K), D264.1 (K), D265.1 (K), D266.1 (K), D267.1 (K), D268.1 (K), D269.1 (K), D270.1 (K), D271.1 (K), D272.1 (K), J1.16
unnamed: D273.1 (K), D274.1 (K), D275.1 (K), D276.1 (K), D277.1 (K), D278.1 (K), D279.1 (K), D280.1 (K), D281.1 (K), D282.1 (K), D283.1 (K), D284.1 (K), D285.1 (K), D286.1 (K), D287.1 (K), D288.1 (K), J1.14
unnamed: D289.1 (K), D290.1 (K), D291.1 (K), D292.1 (K), D293.1 (K), D294.1 (K), D295.1 (K), D296.1 (K), D297.1 (K), D298.1 (K), D299.1 (K), D300.1 (K), D301.1 (K), D302.1 (K), D303.1 (K), D304.1 (K), J1.12
unnamed: D305.1 (K), D306.1 (K), D307.1 (K), D308.1 (K), D309.1 (K), D310.1 (K), D311.1 (K), D312.1 (K), D313.1 (K), D314.1 (K), D315.1 (K), D316.1 (K), D317.1 (K), D318.1 (K), D319.1 (K), D320.1 (K), J1.10
unnamed: D321.1 (K), D322.1 (K), D323.1 (K), D324.1 (K), D325.1 (K), D326.1 (K), D327.1 (K), D328.1 (K), D329.1 (K), D330.1 (K), D331.1 (K), D332.1 (K), D333.1 (K), D334.1 (K), D335.1 (K), D336.1 (K), J1.8
unnamed: D337.1 (K), D338.1 (K), D339.1 (K), D340.1 (K), D341.1 (K), D342.1 (K), D343.1 (K), D344.1 (K), D345.1 (K), D346.1 (K), D347.1 (K), D348.1 (K), D349.1 (K), D350.1 (K), D351.1 (K), D352.1 (K), J1.6
unnamed: D353.1 (K), D354.1 (K), D355.1 (K), D356.1 (K), D357.1 (K), D358.1 (K), D359.1 (K), D360.1 (K), D361.1 (K), D362.1 (K), D363.1 (K), D364.1 (K), D365.1 (K), D366.1 (K), D367.1 (K), D368.1 (K), J1.4
unnamed: D369.1 (K), D370.1 (K), D371.1 (K), D372.1 (K), D373.1 (K), D374.1 (K), D375.1 (K), D376.1 (K), D377.1 (K), D378.1 (K), D379.1 (K), D380.1 (K), D381.1 (K), D382.1 (K), D383.1 (K), D384.1 (K), J1.2
unnamed: D385.1 (K), D386.1 (K), D387.1 (K), D388.1 (K), D389.1 (K), D390.1 (K), D391.1 (K), D392.1 (K), D393.1 (K), D394.1 (K), D395.1 (K), D396.1 (K), D397.1 (K), D398.1 (K), D399.1 (K), D400.1 (K), J1.1
unnamed: D401.1 (K), D402.1 (K), D403.1 (K), D404.1 (K), D405.1 (K), D406.1 (K), D407.1 (K), D408.1 (K), D409.1 (K), D410.1 (K), D411.1 (K), D412.1 (K), D413.1 (K), D414.1 (K), D415.1 (K), D416.1 (K), J1.3
unnamed: D417.1 (K), D418.1 (K), D419.1 (K), D420.1 (K), D421.1 (K), D422.1 (K), D423.1 (K), D424.1 (K), D425.1 (K), D426.1 (K), D427.1 (K), D428.1 (K), D429.1 (K), D430.1 (K), D431.1 (K), D432.1 (K), J1.5
unnamed: D433.1 (K), D434.1 (K), D435.1 (K), D436.1 (K), D437.1 (K), D438.1 (K), D439.1 (K), D440.1 (K), D441.1 (K), D442.1 (K), D443.1 (K), D444.1 (K), D445.1 (K), D446.1 (K), D447.1 (K), D448.1 (K), J1.7
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

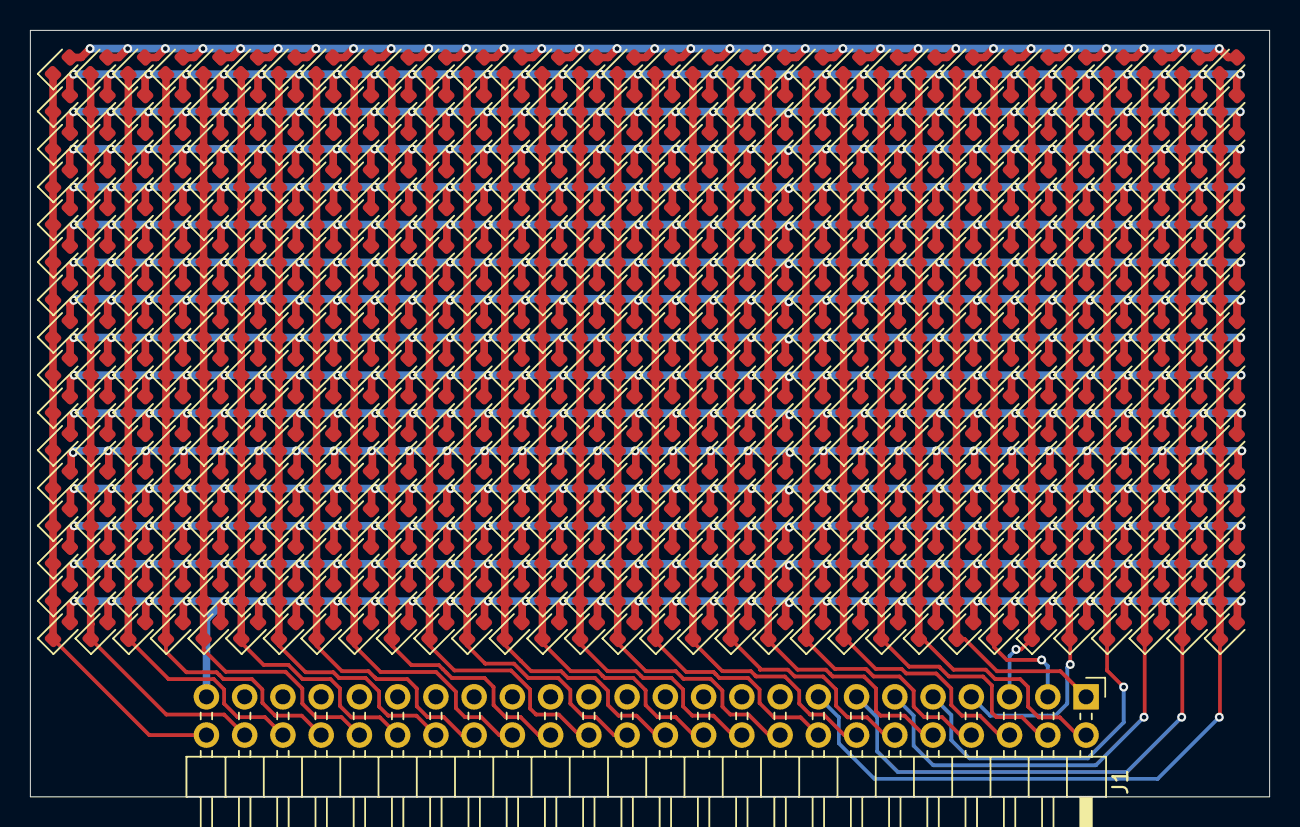
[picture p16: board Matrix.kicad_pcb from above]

Board: 4 copper layers, 82.3 x 50.9 mm, 513 parts (0 on the bottom side), 48 nets.

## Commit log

2024-11-02 all existing work
    [16x32_matrix.kicad_sch, Matrix.kicad_pcb, Matrix.kicad_sch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]
2024-11-02 add files for rieview
    [mainBoard_BOM.csv]
2024-11-10 getting ready for another review
    [Matrix.kicad_pcb, Matrix.kicad_sch, Matrix.step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]
2025-01-31 changes made on laptop
    [mainBoard.kicad_pcb, mainBoard.kicad_sch]
2025-01-31 changes made on desktop
    [mainBoard.kicad_pcb]
2025-01-31 some more files
    [mainBoard_BACKUP_535404.kicad_pcb, mainBoard_BACKUP_535611.kicad_pcb, mainBoard_BACKUP_535721.kicad_pcb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]
2025-01-31 fuck conflicts, just go back to what was on my pc
    [mainBoard.kicad_pcb]
